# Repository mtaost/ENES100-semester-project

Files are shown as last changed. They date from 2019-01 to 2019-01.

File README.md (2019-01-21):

# ENES100 semester project
ENES 100 is an introduction class for all engineering majors and has students work in teams of 8 to construct an autonomous robotic vehicle to traverse a sand arena and complete a set of tasks. 
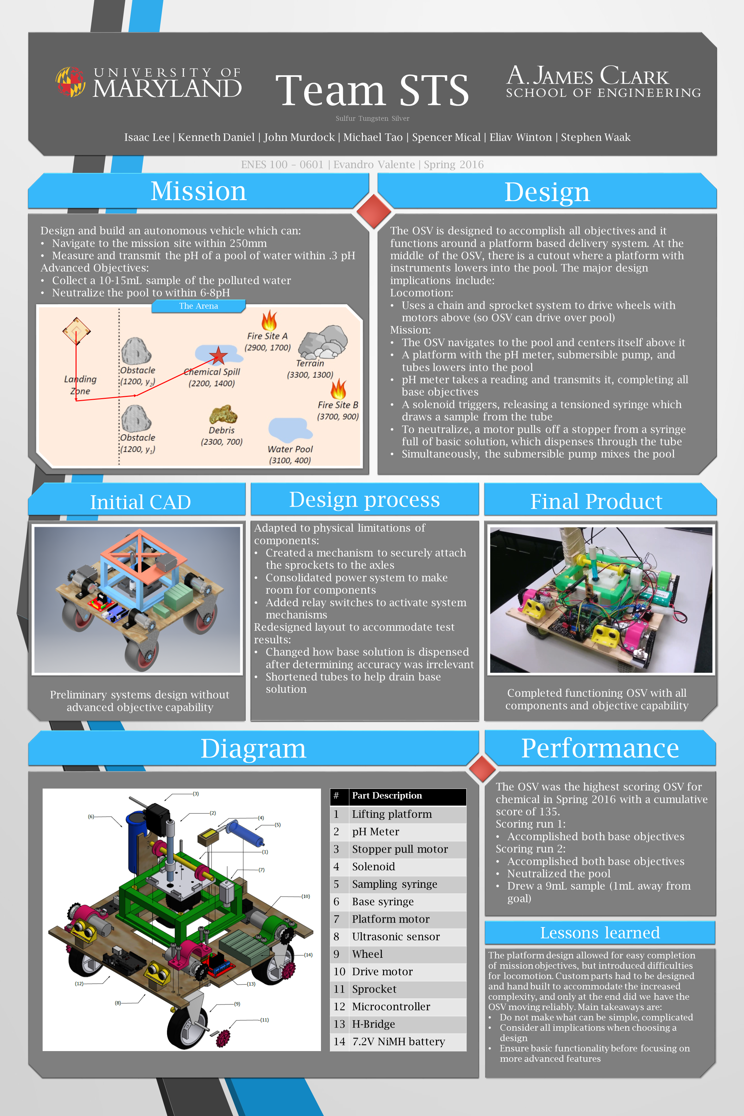
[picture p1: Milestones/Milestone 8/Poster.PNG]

As seen in the poster graphic, the arena was a closed off sandbox with two randomly placed rock obstacles and pre-placed objective sites. Some of the objectives were candles which had to be extinguished or blocks that had to be measured. As our team's mission was the chemical mission, our OSV (On Sand Vehicle) had to:

 - Navigate to the mission objective (a pool of water)
 - Measure the pH of the water and transmit it to the base station
 - Collect a 10-15mL sample of the water
 - Neutralize the pool of water to a pH of 6-8

The class was graded mostly on milestones throughout the class which included presentations and reports detailing our plan of attack as well as the final results. A more detailed description of each milestone can be found at [Milestones/README.md](https://github.com/mtaost/ENES100-semester-project/blob/master/Milestones/README.md) 
My role in this project was team captain so I had a large part in design decisions and task distribution. Ultimately our team succeeded in completing all of our mission objectives.

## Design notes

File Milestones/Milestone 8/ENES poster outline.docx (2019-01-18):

ENES poster outline

- Mission
- OSV details:
  - Locomotion
  - Actuation
- Mission Process
  - How it does the things
  - Control algorithm
- Performance
  - Placement
- Control algorithm
- Design process
  - Initial Cad
  - Final Cad
  - Final picture
- Lessons learned
- Design choices

Executive Summary

Introduction

Shortcomings

Design details:

Structure

Propulsion

OSV Mission

Power

Sensors and Actuators

Control algorithm

Final design drawings

Drawing

Assembly

Circuit diagram

Construction details

Final BOM

Gantt chart

Product performance and evaluation

Lessons learned

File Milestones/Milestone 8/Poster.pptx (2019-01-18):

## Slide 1

Team STS
Sulfur Tungsten Silver

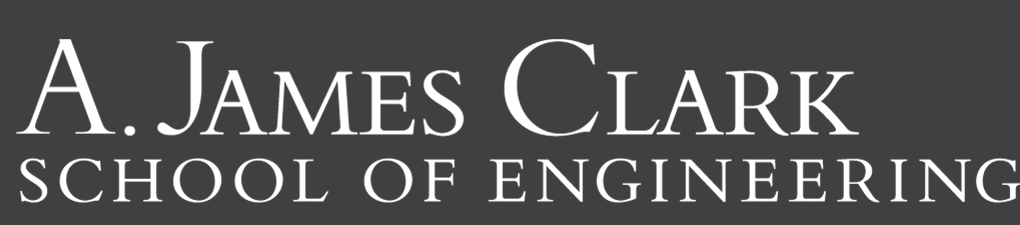
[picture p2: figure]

Isaac Lee | Kenneth Daniel | John Murdock | Michael Tao | Spencer Mical | Eliav Winton | Stephen Waak

ENES 100 – 0601 | Evandro Valente | Spring 2016

Mission

Design and build an autonomous vehicle which can:
- Navigate to the mission site within 250mm
- Measure and transmit the pH of a pool of water within .3 pH
Advanced Objectives:
- Collect a 10-15mL sample of the polluted water
- Neutralize the pool to within 6-8pH

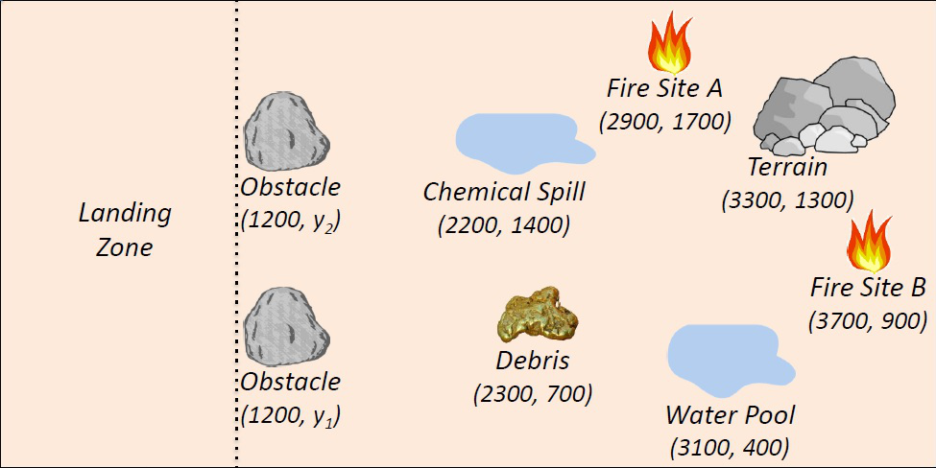
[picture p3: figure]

The Arena

Design

The OSV is designed to accomplish all objectives and it functions around a platform based delivery system. At the middle of the OSV, there is a cutout where a platform with instruments lowers into the pool. The major design implications include:
Locomotion:
- Uses a chain and sprocket system to drive wheels with motors above (so OSV can drive over pool)
Mission:
- The OSV navigates to the pool and centers itself above it
- A platform with the pH meter, submersible pump, and tubes lowers into the pool
- pH meter takes a reading and transmits it, completing all base objectives
- A solenoid triggers, releasing a tensioned syringe which draws a sample from the tube
- To neutralize, a motor pulls off a stopper from a syringe full of basic solution, which dispenses through the tube
- Simultaneously, the submersible pump mixes the pool

Initial CAD

Preliminary systems design without advanced objective capability

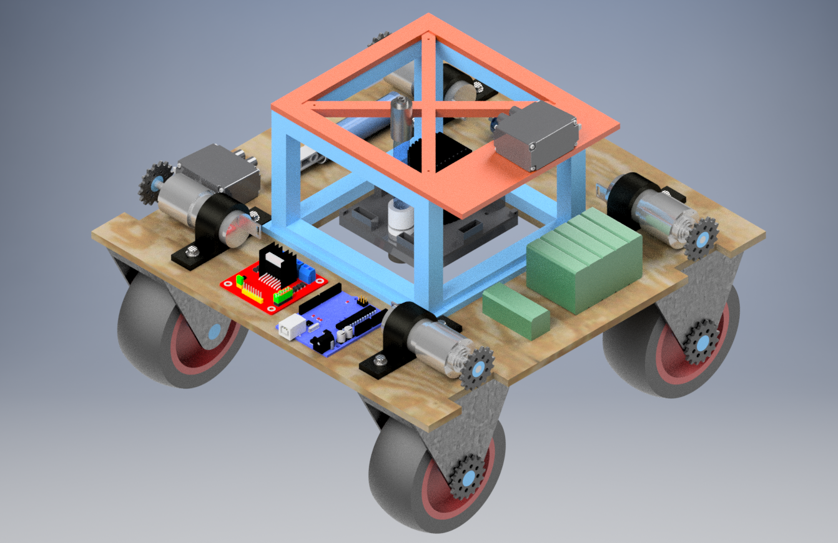
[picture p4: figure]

Design process

Adapted to physical limitations of components:
- Created a mechanism to securely attach the sprockets to the axles
- Consolidated power system to make room for components
- Added relay switches to activate system mechanisms
Redesigned layout to accommodate test results:
- Changed how base solution is dispensed after determining accuracy was irrelevant
- Shortened tubes to help drain base solution

Final Product

Completed functioning OSV with all components and objective capability

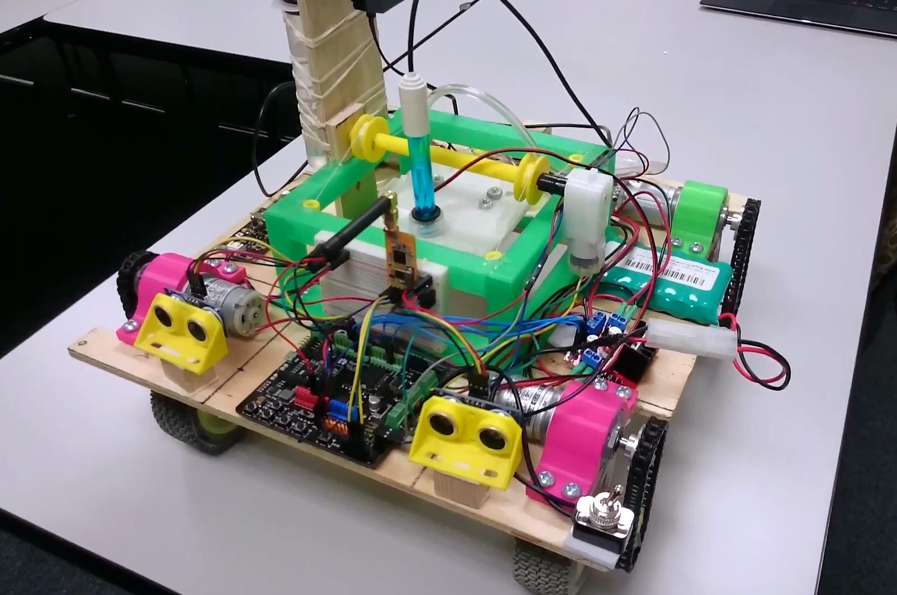
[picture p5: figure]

Diagram

Performance

The OSV was the highest scoring OSV for chemical in Spring 2016 with a cumulative score of 135.
Scoring run 1:
- Accomplished both base objectives
Scoring run 2:
- Accomplished both base objectives
- Neutralized the pool
- Drew a 9mL sample (1mL away from goal)

Lessons learned

The platform design allowed for easy completion of mission objectives, but introduced difficulties for locomotion. Custom parts had to be designed and hand built to accommodate the increased complexity, and only at the end did we have the OSV moving reliably. Main takeaways are:
- Do not make what can be simple, complicated
- Consider all implications when choosing a design
- Ensure basic functionality before focusing on more advanced features

# | Part Description

1 | Lifting platform
2 | pH Meter
3 | Stopper pull motor
4 | Solenoid
5 | Sampling syringe
6 | Base syringe
7 | Platform motor
8 | Ultrasonic sensor
9 | Wheel
10 | Drive motor
11 | Sprocket
12 | Microcontroller
13 | H-Bridge
14 | 7.2V NiMH battery

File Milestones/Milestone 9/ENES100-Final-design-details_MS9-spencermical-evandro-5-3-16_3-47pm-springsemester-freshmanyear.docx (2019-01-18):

Spencer Mical

Team: S.T.S.

Teacher: Evandro

Mission: Chemical Neutralization

Final design details. This should include details of your final OSV design as well as your final mission strategy. Include engineering drawings of the OSV and any components, as well as circuit diagrams as needed to make the description more comprehensible to a reader. Include appropriate calculations and test results either in the body of the section or in an Appendix, as suited for narrative coherence. Include the following subsections.

Structure. Present the size, shape, materials, and construction methods for your structure along with details of your wheel type and suspension. Include estimates or measurements of OSV mass.

Propulsion. Present the sizing and selection of your propulsion system. Include details of wheel or tread size, motor selection, drive train, and steering system design. Provide calculations for the required motor/wheel torque and resulting motor/wheel angular velocity and OSV speed. Provide details of the placement of each of these components. Provide results of performance measurements or tests conducted in the laboratories.

OSV Mission. Identify which mission your OSV attempted and describe your final strategy used to complete the mission. Provide details of the performance of this design strategy.

Power. Present your power system for propulsion and electronic control systems. Describe how you modulated power. Include battery selection details, run-time estimates and actual power subsystem performance.

Sensors and actuators. Present your sensors and actuators, describe how they interact with the Arduino interface, and discuss the rationale for their final placement on your craft.

Control algorithm. Discuss your control strategy and present a flowchart or pseudocode of your control algorithm. In the Appendix, provide the final code generated for your controller. These pages of final code are the only part of the Appendix that do not count towards your 25 page limit. A reader should be able to make sense of how your algorithm functioned.

Final design drawings. Present the following computer-generated drawings with sufficient labels, dimensions and notes. Follow appropriate technical standards. All fonts must be 10 point or larger. Drawings that are appropriate to include within the ‘design details’ section, should be included there. Any that do not fit into the description should be included in this separate section. At the very least, the following three drawings should be included in the report:

- Drawing of OSV structure showing construction detail.
- Assembly drawing of complete vehicle with all components. Clearly identify the location of each component.
- Wiring schematic(s) for all electronic components.

Construction details. Provide the details of the construction materials and processes. Include additional drawings and photos as necessary to allow someone with a similar level of training to regenerate your OSV.

Final design details. This should include details of your final OSV design as well as your final mission strategy. Include engineering drawings of the OSV and any components, as well as circuit diagrams as needed to make the description more comprehensible to a reader. Include appropriate calculations and test results either in the body of the section or in an Appendix, as suited for narrative coherence. Include the following subsections.

Team S.T.S. O.S.V. was designed to meet the maximum parameters of the competition. In doing so, the O.S.V. was designed to have a wide body width and length. This design was purposeful, as it allowed the O.S.V. to drive over the chemical water source, stop on top of the objective, and lower a platform into the pool of water. The body of the O.S.V. has a square-section cut out of the middle, which enables the lifting platform to be lowered from the O.S.V. body to the water, and then raised back up from the water to the O.S.V. body. The lifting platform is attached to a C.A.D.-designed and printed mount/box, which provides support and stability for the lifting platform as it elevates and sinks. Also attached to the O.S.V. body are four motors, each secured to the O.S.V. body by C.A.D. modeled motor mounts. These motors provide power to the four wheels that propel our O.S.V., which are located on the underside of the vehicle.

Pertaining to the mission strategy, team S.T.S. used two ultrasonic sensors, which are mounted to the front of the vehicle. These, along with the control algorithm, enabled the O.S.V. to navigate from the landing zone to the polluted pool, while simultaneously avoiding obstacles. Upon arrival to the pool, the O.S.V. would park over the objective, and would then run a program which controls the crank that raises and lowers the lifting platform. The lifting platform will then be lowered into the water, where all of our base objectives will be met. After successfully navigating to the pool site, and thus accomplishing the first base objective, the lifting platform will then rise back up to the O.S.V. body. The platform will then lower again, and the pH meter will be inserted into the water. At this point, the pH meter will record the pH, satisfying the second basic objective. Upon determining the pH, the pH meter will inform the A.P.C. what the pH is, and then the A.P.C. will transmit the pH to command. After fulfilling the base objectives, additional instruments that are mounted on the O.S.V. body will perform the advanced objectives. There are two syringes attached to the O.S.V.’s body: a 10 mL syringe, which is used to extract a 10 mL sample of polluted water, prior to the team’s neutralization of the pool of water, and a 50 mL syringe, which has a tube attached to it. The 10 mL syringe is constrained by solenoid, which, upon a signal, will retract. Once the solenoid has moved back, the syringe will begin extracting the sample of water, and also completing the first advanced objective. Then, the 50 mL syringe is activated, as part of the second advanced objective of neutralizing the water source. The lifting platform will facilitate a base to be added to the acidic water, via a tube that connects a syringe that’s mounted on the O.S.V. body to the water source. A pump also housed on this platform would be activated, and would agitate the water as the base was dispensed, thus expediting the neutralization process, and accomplishing the second advanced objective.

Structure. Present the size, shape, materials, and construction methods for your structure along with details of your wheel type and suspension. Include estimates or measurements of OSV mass.

Team S.T.S.’s O.S.V. is a square, measuring 350 mm by 350 mm, with a body thickness of 6.13 mm. There is a square hole cut out of the center, as previously mentioned, which allows for the lifting platform to raise up and down.

The O.S.V. body is composed of wood. The majority of the other assembled parts that were subsequently attached to the O.S.V. are either wood, metal, or P.L.A. Wood was used to fasten and secure certain instruments down to the body of the vehicle. Metal was used as a wheel holder to ensure that the wheels are straight and secure, which ensures accuracy in the vehicle’s movement. P.L.A. was used as a result of C.A.D. 3D parts, which were constructed to meet certain parameters and dimensions, and then printed and added to the OSV body.

The O.S.V. weighs approximately 2700 grams without the base solution loaded into the syringe.

OSV Mission. Identify which mission your OSV attempted and describe your final strategy used to complete the mission. Provide details of the performance of this design strategy.

Team S.T.S.’s mission was the chemical neutralization mission. The basic objectives were to navigate to within 250 mm of the polluted freshwater pool, much like the first basic objective of every other group, as we had to navigate to within 250 mm of our objective. Our second basic objective was to measure the pH level of the polluted freshwater pool, and our third basic objective was to transmit that pH level back to command. Our advanced objectives were to collect a 10-15 mL sample of the polluted freshwater source, prior to neutralizing the pool pH to a range of 6 - 8. We would then have to transmit this neutralized pH back to command to complete the second advanced objective.

In the first run, the O.S.V. completed all of the basic objectives. It navigated directly to the polluted freshwater pool after a brief interaction with a boulder. The O.S.V. then proceeded to park atop the polluted freshwater pool, per the group’s design. The lifting platform, containing a pH meter was lowered into the pool, where it acquired and transmitted the pH of the pool back to command. When the O.S.V. attempted to do the advanced objectives, a few things went wrong, and neither of the two were completed. Pertaining to the 10-15 mL sample, the O.S.V. had a syringe that had been stopped by a solenoid. When the solenoid fired, the syringe would retract, and would thus take up water with it. During the first run, the solenoid never fired, so the syringe never extracted water. Regarding the neutralization process, the O.S.V. was intended to administer a sodium bicarbonate base to the acidic pool. However, the base was added to the O.S.V. too early, and it solidified on the bottom of the syringe, thereby blocking any flow of water or base into the pool. All in all, the O.S.V. received a 60/60 for performing all of the basic objectives.

For the second run, things went much better. Again, the O.S.V. accomplished all of the basic objectives. It successfully navigated to the polluted freshwater pool, after temporarily getting stuck on a boulder. Through sheer power, the O.S.V. broke past, and went on to complete the mission. The O.S.V. stopped over the pool, and once again lowered the lifting platform into the water. The pH meter recorded and transmitted the pH of the acidic pool back to command, thus securing another perfect basic objective performance. However, the O.S.V. then went on to successfully complete the two advanced objectives as well. The solenoid fired properly this time, as an acceptable sample of water was collected (up to debate between the judges and our team). Additionally, the neutralization process went according to plan. The base was administered to the O.S.V. moments before the second run began, so it wouldn’t have time to settle and solidify. The syringe with base released a pre-measured amount of base and water into the pool, where the pH of the pool was neutralized from a pH of 2.99, to a pH of 6.31, thereby successfully completing the second advanced objective.

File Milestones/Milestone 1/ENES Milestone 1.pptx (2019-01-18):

## ENES Milestone 1

Team STS (Sulfur Tungsten Silver)

## Team Roster

- Isaac Lee (The neutralizer)
- Kenneth Daniel (Canned denial)
- Michael Tao (Chairman Tao)
- John Murdock (John Cena)
- Eli Winton (Wins a ton)
- Spencer Mical (One man army)
- Stephen Waak (Woah, OK)

## Mission objectives

- Chemical Team:
  - Base Objectives:
    - Navigate to within 250 mm of the polluted freshwater pool
    - Measure the pH level of the pool
    - Transmit to command the pH level to within 0.3 units
  - Advanced Objectives:
    - Collect a 10 – 15 ml sample of the polluted water prior to neutralization
    - Neutralize the pool by returning the pH level to the range of 6 - 8 and transmit to command the final pH level

## Team Structure

Project Leader: Michael Tao
- Subgroups:
  - Mechanical : Isaac Lee
    - CAD: Kenneth Daniel
  - Electrical: John Murdock
  - Programming: Michael Tao
Meeting arrangements:
  - After class in JMP on Thursday
  - Otherwise, Hornbake or McKeldin

## Design Concepts - Structure

- 4x4 design without suspension
- Wheel width and diameter is being determined with respect to desired torque
- Designing base for maximum size (350mm x 350mm)
- Wooden base platform, 3d printed support

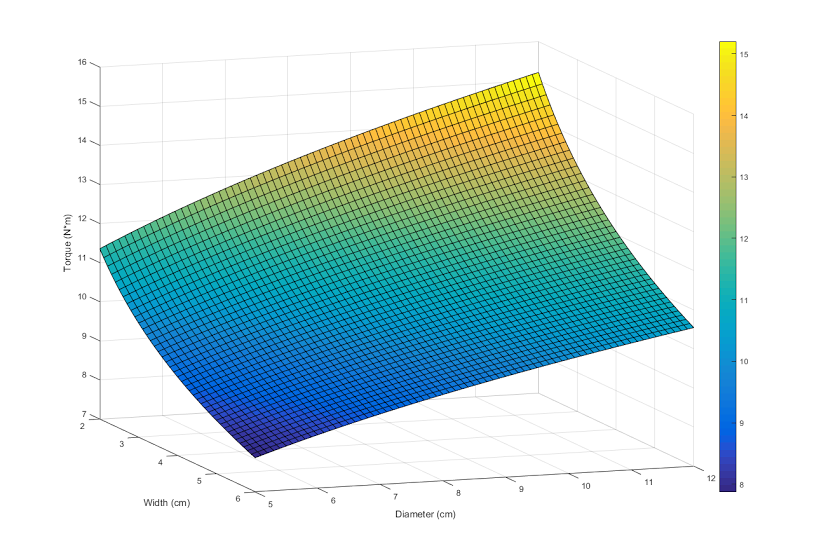
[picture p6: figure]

## Design Concepts - Structure

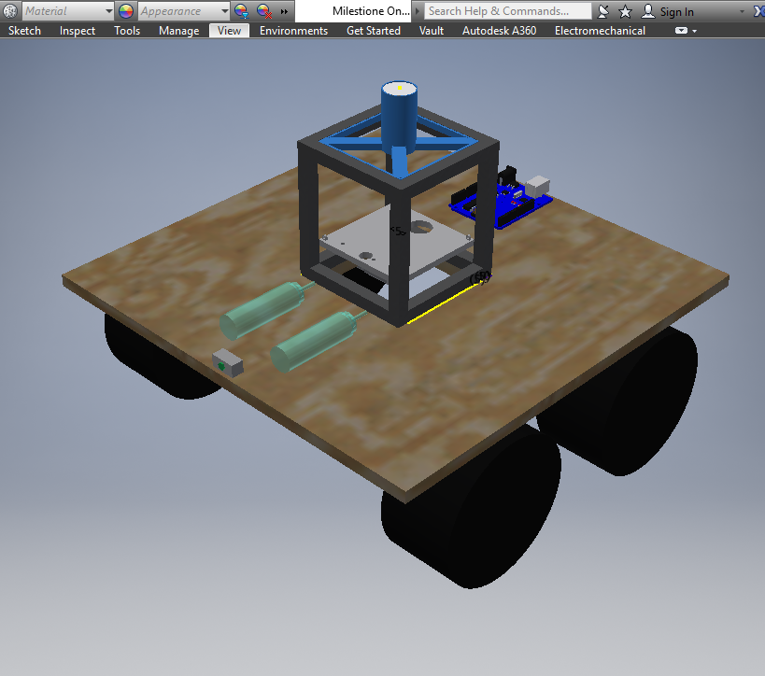
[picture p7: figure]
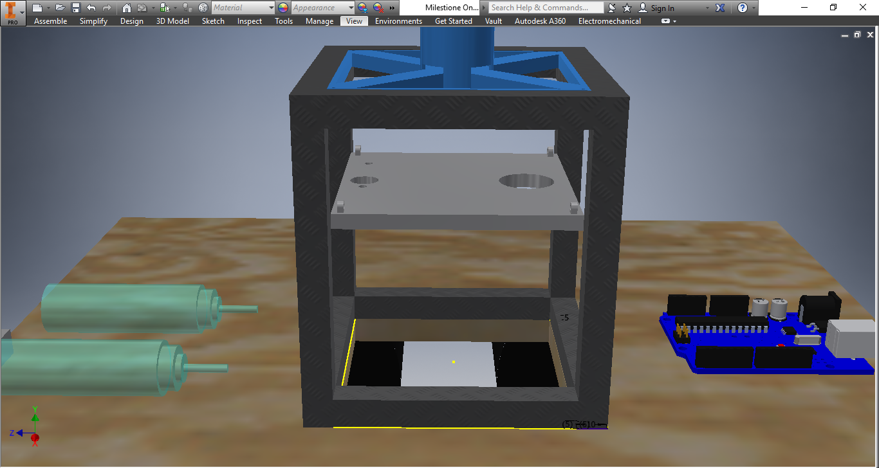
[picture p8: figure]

## Design Concepts - Mobility

- Torque required in one rear wheel τ=TE∙r TE=C_(RR) ∙F_N C_(RR) =[3.33(cm^3)/N∙(F_N)/(w∙d^2)]^(1/3)
F_N =(lmgcosθ+hmgsinθ)/(4l)
r = wheel radius
w = wheel width
d = wheel diameter
h = height of center of mass
m = mass of OSV
g = acceleration due to gravity
ϴ = angle of inclination
l = horizontal distance from contact point to center of mass

## Design Concepts - Mobility

- Using assumed values, r = 6.4cm w = 6cm d = 12.8cm h = 10cm m = 2.5kg g = 9.8 m/(s^2) 30° < ϴ < 40° l = 11.1cm  15.54 N∙cm<τ<15.99 N∙cm Minimum torque required for rear wheel rotation up an incline

## Design Concepts – Avoiding The Dig

0.3F_N <TE<0.7F_N
0.3F_N ∙r<τ<0.7F_N ∙r
The limiting scenario would be at 0°
Using previous assumptions,
11.76 N∙cm<τ<27.44 N∙cm
Torque range required to not dig sand at 0°
15.99 N∙cm<τ<27.44 N∙cm
Torque range required to move up 40° inclines but not dig sand at 0°

## Design Concepts - Mobility

- Based on our calculations of our range of τ , we have found 2 motors that fit our needs, both of the same form factor but with a different transmission
- Both are planetary

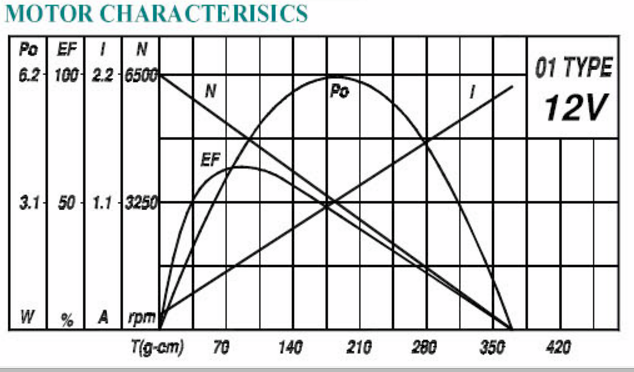
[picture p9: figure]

## Design Concepts - Mobility

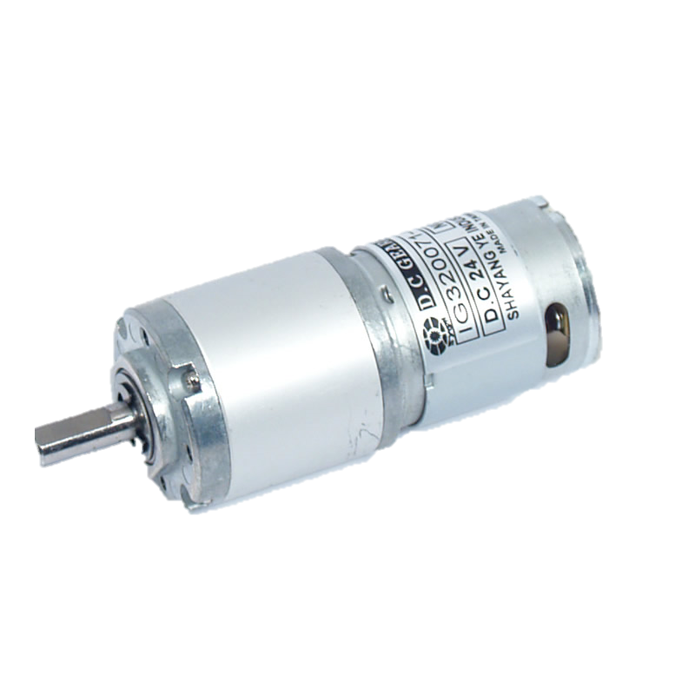
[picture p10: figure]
IG32 12VDC 104 RPM Gear Motor

Torque: 45.08 N*cm
RPM: 53
Gear ratio: 1:100
Voltage: 12V
Max I draw: 530mA
Mass: 190g

Torque: 22.54 N*cm
RPM: 104
Gear ratio: 1:51
Voltage: 12V
Max I draw: 530mA
Mass: 190g

## Design Concepts - Power

- At maximum power, both of the motor choices will draw 530mA, so max current of 4 motors is 2.12A
- Assuming the other systems draw 100mA, we have a total current draw of 2.22A
- If we want a run time of 1 hour, we need a battery at 12V with a capacity of at least 2.22Ah

## Design Concepts - Power

- 12 V 2200mAh battery with built in short circuit protection

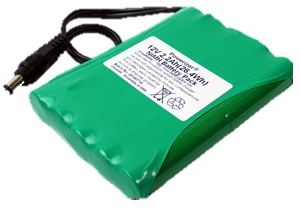
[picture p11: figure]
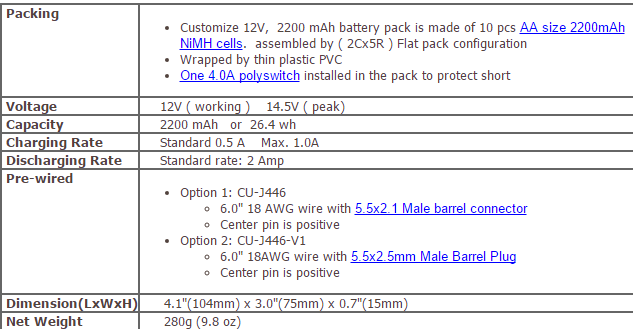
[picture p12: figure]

## Design Concepts – Mission performance

- Platform driven directly over pool to perform mission objectives
- pH probe on platform to be lowered into pool
- Motor driven syringe to obtain sample
- Motor driven syringe to inject neutralizer solution
- Electric submersible pump to agitate solution
- Closed feedback loop to neutralize solution to pH 7

## Design Concepts - Navigation

- Differential drive with the 4x4 motors
- Using an array of ultrasonic sensors to locate obstacles
- Contact sensors or color sensors underneath the OSV to detect the pool of water

## Gantt chart

## Anticipated problems

Problems
- Inability to focus on task during meetings
- Individual tasks not being completed by deadline
- Electronics malfunctioning (Releasing magic smoke / mechanical failure)

Solutions
Create defined goals for each meeting
Enact consequences for failing to meet deadlines (Voluntary sponsored pizza dinner)
For cheaper parts, always buy an extra. Have someone else check wiring before powering on

## Anticipated problems

Problems
- Member unable to contribute due external reasons
- Unequal work distribution

Solutions
Redistribute tasks to best ability
Discuss how work could be divided evenly but still adhere to standards

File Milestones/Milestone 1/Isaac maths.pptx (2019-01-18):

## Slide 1

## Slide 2

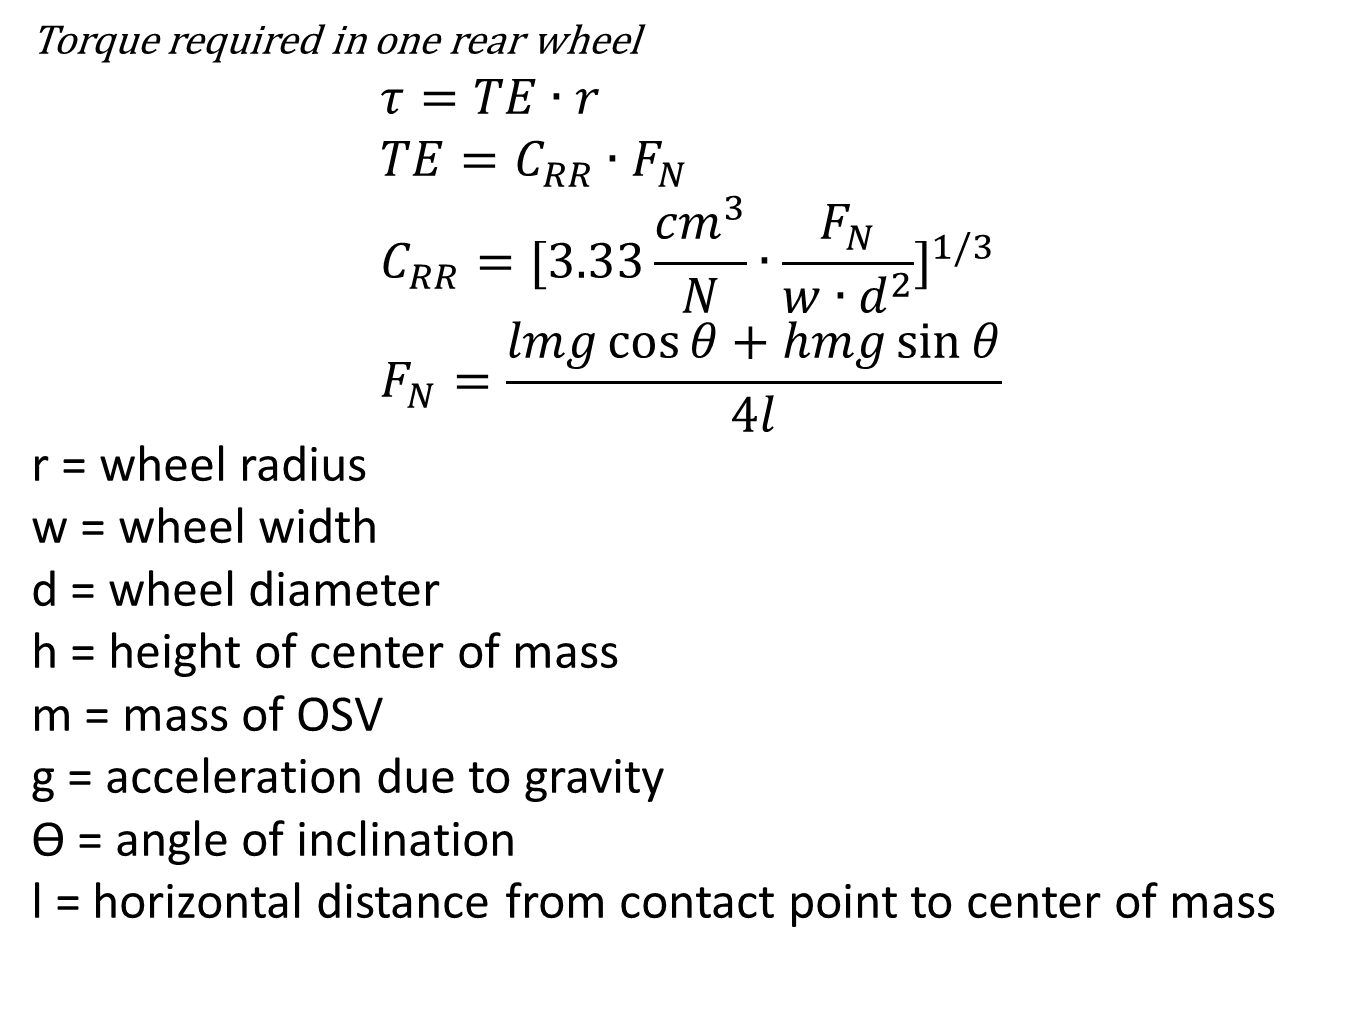
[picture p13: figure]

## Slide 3

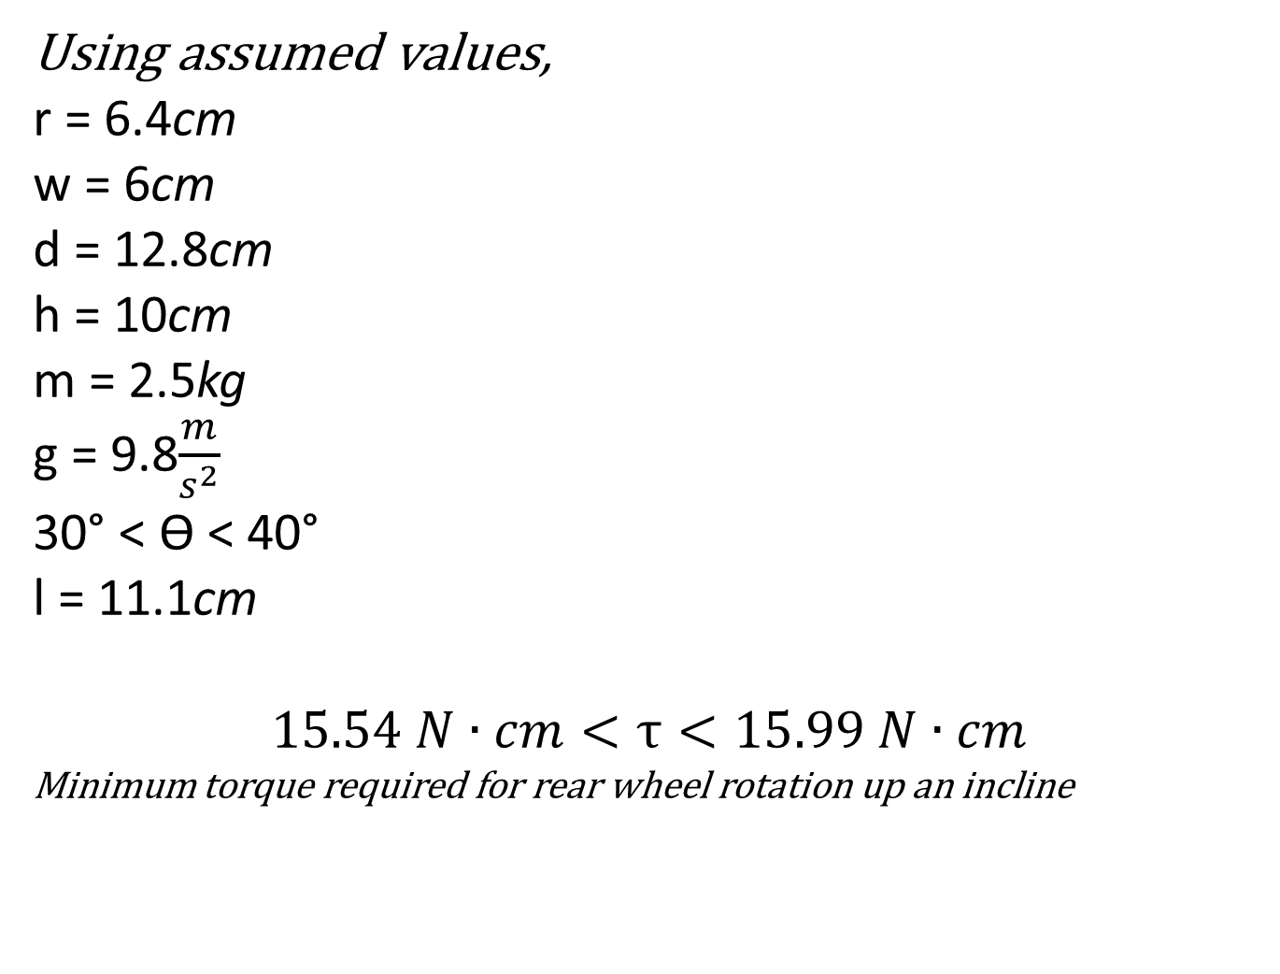
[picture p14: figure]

## Avoiding The Dig

0.3F_N <TE<0.7F_N
0.3F_N ∙r<τ<0.7F_N ∙r
The limiting scenario would be at 0°
Using previous assumptions,
11.76 N∙cm<τ<27.44 N∙cm
Torque range required to not dig sand at 0°
15.99 N∙cm<τ<27.44 N∙cm
Torque range required to move up 40° inclines but not dig sand at 0°

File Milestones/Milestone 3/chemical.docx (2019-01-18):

For our chemical neutralization mission our primary objective is finding and neutralizing a pool of water within the given amount of time. We are required to navigate within 250 millimeters of a polluted fresh water pool with the water being between 650 and 850 milliliters and the pollution being between 2 and 5 pH. Once we reach the pool we must measure the pH level of the pool and report back to command the pH level to within 0.3 units. After testing the pH level we must then extract a 10-15 milliliter sample of the polluted water. Once we have successfully collected the sample of water we can then begin to neutralize the pool and bring the pH level back to between 6 and 8 and report our level to the command.

To navigate to the pool, we will use distance sensors and angular turning to navigate around the obstacles. After the obstacles are cleared, the OSV will drive to the coordinates of the pool. Once over the pool, the OSV will lower the inner platform into the pool. From here it will extract the sample of the polluted water, measure the pH of the pool, and send the pH reading back to base. After this part is complete, the OSV will dispense the fully saturated sodium bicarbonate solution until the pH of the pool reaches 6 using a closed feedback loop. While the base is being dispensed, the pump will be agitating the pool to mix in the base. Once the pH meter reads a pH within the range of 6 to 8, the OSV will stop dispensing base and will report the measured pH to base.

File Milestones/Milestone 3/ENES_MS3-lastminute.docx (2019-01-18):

The O.S.V. is approximated to be at the full 350 mm by 350 mm, although if it can be slimmed down a bit that will be attempted. The O.S.V. will feature a wooden platform that measures 350 mm by 350 mm, and upon that will be everything that the O.S.V. needs to operate. The O.S.V. will include four motors, an Arduino Romeo board, and an H-Bridge to connect a 12 volt battery to the wheels. A 7.2 volt battery will provide power to the rest of the O.S.V.

The O.S.V. has a box-like structure. The main body platform is a large square. On top of that, at the center of the large square, is a hollowed out cube, which houses and will help operate the lifting platform.

The O.S.V. will be constructed over several weeks. Parts will be added meticulously and cautiously, in order to ensure that they are placed accurately and are securely fasted/attached to the O.S.V.

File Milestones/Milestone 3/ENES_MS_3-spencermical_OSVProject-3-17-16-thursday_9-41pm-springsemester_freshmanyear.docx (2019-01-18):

ENES MS 3

For Spencer’s portion of MS 2 and MS 3, Spencer worked on CAD designs and doing some research on the chemical aspects of the O.S.V. project. Spencer also took measurements to determine the mass, volume, and areas, of multplie components of the O.S.V. Additionally, Spencer and Isaac came up with the idea that the O.S.V. would drive and park over the polluted water source, and then lower the pH and base solutions into the water.

Ken would dimension parts for the O.S.V. that had to be CADded, and Spencer would CAD them. Ken and Spencer about equally split the amount of CADding for the O.S.V., but Ken is the one who assembled all of the parts together to make one-coherent viewing of the O.S.V. as it is in the presentation. Ken would give Spencer an idea of a part that the O.S.V. needed, and Spencer would create it. Otherwise, Ken would give Spencer dimensions or other parameters that needed to meet O.S.V. specifications, and Spencer sought out to create a part that could fit those dimensions. After Spencer created the part, Spencer would then determine the area, volume, and estimated mass of these parts, given the density and mass of polylactic acid (P.L.A.). That way, the group could have a decent idea of how much everything would weigh, and therefore could stay within the given parameters of the project. There were also times where Ken gave Spencer dimensions for a part that would later either be scrapped, or re-written/constructed, with new dimensions. Either Ken or Spencer would create this new part. This dynamic duo came through clutch with the CADding for this O.S.V. Although the O.S.V. is currently slightly over the permissable mass, this will be resolved by reducing the battery capacity.

Pertaining to the chemical portions of the project, Spencer determined the density, molarity, molar masses, normality, substance pH, and chemical composition. Based on Spencer’s calculations, this aided Stephen in the chemical portion of the project. Stephen would go on to determine how many grams of base the O.S.V. would need to neutralize varying concentrations of acetic acid in the polluted water environment.

One of Spencer’s initial sketches included a diagram that depicted the O.S.V. lowering the pH indicator and the base dispensor into the water. Isaac, too, initally had this idea. The two of them convinced the group that this was plausible, and left little room for error in approaching the water source (i.e. getting to within 250 mm of the objective wouldn’t be difficult). This is the approach that the group has chosen to operate with. Some difficulties may include interference with the wheel motors and the water-source, but this is to be remedied by sticking the motors on top of the platform.

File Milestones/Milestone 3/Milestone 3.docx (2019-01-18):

ENES 100

Section 0601

Milestone 3

Team STS - Chemical

Table of Contents

Page
2 | Team contributions
3 | Executive Summary
4 | Introduction
5-6 | Design: Structure
7-11 | Design: Propulsion
12 | Design: OSV Mission
13-15 | Design: Power
16 | Design: Sensors and actuators, Control algorithms
17 | Design: Control Algorithms
18-22 | Preliminary Design Details
23 | Bill of materials
24 | Gantt chart
25 | Construction plans and anticipated difficulties

Team contributions

John Murdock

Stephen Waak

Eliav Winton

Spencer Mical

Kenneth Daniel

Isaac Lee

Michael Tao

Executive Summary

Our team has designed a vehicle to carry out the chemical neutralization of a pool of water in a sandy terrain. The OSV must fit within a 350mm x 350mm footprint. Overall mass must not exceed 3kg and overall cost of the OSV can be at most $350. With these constraints in mind, we have designed an OSV with four wheels and a lowering platform which will drop into the pool of water to carry out its mission.

For mobility, we have a four wheeled footprint driven by a chain and sprocket. Motors will be mounted above the base of the platform to avoid impacting the pool of water. This will keep the motors safe from the acid pool and leave enough clearance for the bottom. Through control algorithms and sensors, the OSV will navigate autonomously to the pool while avoiding obstacles along the way.

Once the OSV has driven over the pool, it will lower a platform to carry out its mission objectives which include taking a sample, transmitting the pool’s pH, and neutralizing the pool.

Introduction

To fulfill the chemical mission objectives of measuring the pH of a pool, taking a sample, and neutralizing the pool, team STS has designed an OSV that can accomplish these tasks. Locomotion is enabled with four planetary geared motors running at 12v. Each of these motors is mounted atop a wooden base which will serve as the platform for all electronics including microcontroller, motor driver, batteries, and mission specific equipment. Four wheels mounted underneath the platform are connected to sprockets and will be driven through chain by the drive motors. This is to ensure that there is enough clearance beneath the OSV to drive over the pool. Drive motors are driven by a 12v NiMh 2200mAh battery, while microcontroller logic will use a separate 7.2v NiMH 2200mAh battery.

In moving to the mission site, the OSV will navigate using information provided through the APC220, a radio communication module. For obstacle detection, three ultrasonic sensors will be mounted on the front of the OSV so it can detect obstacles in a 45 degree cone in front of it. Through control algorithms, it will avoid obstacles while navigating to the site by determining any obstacles ahead of it and where they are based on proximity.

Once the OSV navigates to the mission site, it will deploy a platform with instruments used to fulfill mission objectives. This platform is held in the center of the OSV and will be further described in technical drawings. On this platform are the pH meter, a pump, and two tubes used to dispense neutralizer, and extract a sample. First, this platform will lower using a smaller geared motor. Then, a sample will be drawn by releasing a spring loaded syringe. Simultaneously, the pH will be read and transmitted back to base through the APC220. Once the base mission objectives are fulfilled, it will then begin dispensing neutralizer. The rate at which the neutralizer is dispensed will be proportional to the difference between desired and actual pH. During this period, the pump will be powered to agitate the solution, thus accelerating the neutralization process and allowing for a more accurate measurement. Once the pool is within acceptable pH ranges, the OSV will have completed all objectives.

Design Details

Structure

The O.S.V. is approximated to be constructed at the full 350 mm by 350 mm and then sanded down to allow for a safe margin. The O.S.V. will feature a wooden base that spans this square, and on this base will be the electronics for locomotion and mission specific hardware. Electronics will be secured to the base with screws where possible and mounting brackets if needed. Any 3d printed parts will be secured using wood glue after properly scoring both contact surfaces to allow for proper adhesion.

Our wheels will be 4-inch diameter rubber tires mounted upon 3d printed wheel inserts. These wheels feature small indentations which will help the wheel grip on to the sand better, and they will be attached to sprockets. The motors will then drive the wheels through a chain. We will not use suspension because of cost and complexity.

The O.S.V. has a box-like structure. The main body platform is a large square. On top of that, at the center of the large square, is a hollowed out cube, which houses the lifting platform and allows for its vertical movement. This platform and the supports will be 3d printed which will allow for lightweight construction yet still maintaining structural rigidity.

Mass estimation table

Item | Mass (g) | Quantity | Total mass (g)
12V battery | 280 | 1 | 280
7.2v battery | 125 | 1 | 125
Vex Motor | 87.1 | 1 | 85.5
Sprockets | 2.8 | 8 | 22.4
Base Solution | 150 | 1 | 150
Wooden base | 400 | 1 | 400
Pump | 50 | 1 | 50
pH monitor | 20 | 1 | 20
Lifting Platform | 33.8 | 1 | 33.8
Arduino | 20 | 1 | 20
Wheels | 10 | 4 | 400
Motor | 160 | 4 | 640
Platform counterbalance | 50 | 5 | 250
Total | | | 2565.4

Propulsion

Στ=Iα

F_T ∙r-τ_w =0

F_T ∙r=τ_w

R_x

R_y

τ_w

m_w g

F_(RR)

F_T

F_N

Figure 1. Torque equilibrium. Resultant of F_N and F_(RR) points directly at wheel center

R_x

R_y

τ_w

m_w g

F_(RR)

F_T

At constant velocity,

X:ΣF=ma

F_T -F_(RR) =0

F_T =F_(RR)

F_N

Figure 2. Horizontal forces equilibrium. τ_w , R_y , R_x , m_w g are internal forces.

l

h

mg

F_(Nr)

F_(Nf)

F_(τr)

F_(τf)

x

y

F_(RRr)

F_(RRf)

l

θ

At stall,

X: ∑ F=ma 2F_(τr) +2F_(τf) -mgsinθ-2F_(RRr) -2F_(RRf) =0

Y: ∑ F=ma 2F_(Nr) +2F_(Nf) -mgcosθ=0

Torque from contact point of front wheels

τ :∑ τ=Iα lmgcosθ+hmgsinθ-4lF_(Nr) =0

Figure 3. Equilibrium equations for OSV stalling on an incline.

τ=F_(τr) ∙r

F_(τr) =F_(RR) =C_(RR) ∙F_(Nr)

C_(RR) =[3.33(cm^3)/N∙(F_(Nr))/(w∙d^2)]^(1/3) F_(Nr) =(lmgcosθ+hmgsinθ)/(4l)

Equation 1. Stall torque in one rear wheel on an incline.

TE<0.7F_N

τ<0.7F_N ∙r

Equation 2. Tractive effort and torque maximum to avoid digging into the sand.

RPM(τ)=-65/219τ+65

Figure 4. Motor Torque vs RPM found by converting the motor’s data sheet using a reductioin ratio of 100 and an efficiency of 60%.

It was decided that the wheels must be 3d printed because the design calls for a very narrow range of dimensions that could not be fulfilled by any wheels on the market. The wheel dimensions were chosen to allow the OSV to clear the pool of water and take the platform above the water. The diameter was calculated with the height of the pool in mind, and the width was calculated with the dimensions of the OSV versus the diameter of the pool in mind. The width was optimized for sliding over sand while still allowing the OSV to drive over the pool. It was decided that the diameter of the wheels would be 107mm and the width 44mm. The wheels will be placed 11.15cm away from the center of mass, measured in the direction of motion, and 1cm inward from the edge of the OSV to allow for the chain and sprocket system. They will be housed in two-sided wheel housings to hold them in the same orientation.

The torque calculations were derived with the models depicted in figures 1, 2, and 3. Equation 1 was used with the following dimensions: a radius r of 5.35cm, a width w of 4.4cm, a diameter d of 10.7cm, a height h of the center of mass of 11cm, a mass m of 3kg, an acceleration g due to gravity of 9.8 m/(s^2) , an angle of incline ϴ of 35°, and a length ℓ between the center of mass and center of a wheel of 11.15cm. Using this equation, the minimum torque per wheel required was determined to be 22Ncm. Using equation 2, the maximum torque that could be output to avoid digging into the sand was found to be 27.5Ncm at 0°. Only the scenario with a 0° incline was considered because it was determined that the wheels digging on an incline would not be a problem. The digging would reduce the incline since the front wheels would begin to dig the sand before the rear wheels. Using these parameters, a 12V motor with a rated torque of 46Ncm was chosen. Each wheel would have its own motor. The motor has a variable torque and angular velocity. Since the maximum torque required for OSV operation is lower than the torque at which the wheels begin digging the sand, it was determined that this motor would always operate under the torque for digging, yet always be able to provide enough torque to overcome the sand and any inclines of the sand.

The drive train was designed with the platform mechanism in mind. It was determined that the motors and wheels must be separated so that the motors would not be in the way of the OSV successfully getting over the pool. To achieve this, the four motors would be placed on the base of the OSV and drive the wheels using a system of chains and sprockets. The sprockets would be sized at around a 1:1 ratio initially but, because of the need to reduce OSV velocity, may end up being around a 1:3 ratio. The chains and sprockets would be oriented to the outside of the OSV, so that there will be maximum clearance on the inside to fit the pool between the wheels. Using the torque vs. RPM graph in figure 4 and a wheel radius of 5.35cm, the range 32.7(cm)/s≤v≤34.1(cm)/s was obtained for OSV velocity for between operation at 35° and at 0°, with 1:1 sprockets. With a wheel sprocket that is 3 times wider than the motor sprocket, a theoretical mechanical advantage of 3 is introduced. This means that the torque output is 3 times the torque input and the angular velocity output is one-third the angular velocity input. The wheel would still need the same torque to overcome its resistance, so the motor would output much less torque. This would increase the angular velocity of the motor because angular velocity is inversely proportional to torque. However, as seen in figure 4, reducing the torque by a third does not increase angular velocity threefold because the two quantities are related by a constant. Overall, this design is expected to reduce the angular velocity, and thus the OSV velocity, by approximately 50%, while lightening up on motor current draw due to the lower motor torque requirement.

The steering system will be differential steering and not require any servos. It will turn by adjusting the relative speeds of the different wheels. Pulse-width modulation will be used to lower the angular velocity of certain motors. This can be performed at the motor bridge and be controlled by the Arduino. PWM can be used to proportionally lower the effective current and voltage that is applied to the motor. The motor will then draw more current at the battery to produce the same torque, but its voltage will be lower and be constant. Torque is directly proportional to current because current produces the magnetic field inside the motor that drives the motor shaft. However, angular velocity is directly proportional to voltage because motor voltage is used to overcome the counter-electromotive force produced by the rotor spinning through the motor’s magnetic field. The motors that need to slow down will be fed lower voltage and therefore output a lower angular velocity at the cost of requiring higher current draw to produce the same torque. However, this will not impact battery capacity requirements because the increased current draw is balanced out by the <100% duty cycle, and total power draw will be roughly the same.

OSV Mission

For our chemical neutralization mission, our primary objective is finding and neutralizing a pool of water within a five minute window. The OSV is required to navigate within 250 millimeters of a polluted water pool with the water being between 650 and 850 milliliters and the acidity being between 2 pH and 5 pH. Once it reaches the pool we must measure the pH level of the pool and report back to command the pH level to within 0.3 units. After testing the pH level it must then extract a 10-15 milliliter sample of the polluted water. Once we have successfully collected the sample of water we can then begin to neutralize the pool and bring the pH level back to between 6 and 8 and report the newly adjusted pH to the command.

To navigate to the pool, the OSV will use distance sensors and differential steering to navigate around the obstacles. After the obstacles are cleared, the OSV will drive to the coordinates of the pool. Once over the pool, the OSV will lower the inner platform into the pool. From here it will extract the sample of the polluted water, measure the pH of the pool, and send the pH reading back to base. After this part is complete, the OSV will dispense the fully saturated sodium bicarbonate solution until the pH of the pool reaches 6 using a closed feedback loop. While the base is being dispensed, the pump will be agitating the pool to mix in the base. Once the pH meter reads a pH within the range of 6 to 8, the OSV will stop dispensing base and will report the measured pH to base.

Power

For our power system, we used two separate batteries. The battery that we will be using to power the Romeo Board is a 7.2V 2200mAh NiMH battery. This will provide power for all mission specific hardware. The battery that is used to power the wheel motors is a 12V 2200mAh NiMH battery. These batteries were chosen because they are able to supply power within the operational limits of the electronics necessary for function and sustain that power for a long enough time.

The 12V battery will connect to the H-bridge that connects to the four drive motors. Calculating the current draw of the four motors used to power the wheels in the OSV is dependent on the amount of torque that is required in each of the wheels. As previously stated, the amount of torque required will depend on the angle of the wheel the motor is attached to with respect to ground level. Once this is known, determining the current can be done by using the equation:

i = mτ + b

Equation 3. Current draw at a given motor torque

In this equation, i is the current draw, m is the motor torque constant which is equal to 11.78mA/Ncm or the max current of 530mA divided by the stall torque of 45Ncm, τ is the torque, and b is the no load current of 150mA. This allows us to determine the range of currents that are possible. Based on the previous torque calculations:

Minimum torque required: 14.3Ncm

Maximum torque required: 22.2Ncm

And using equation 3 to find the minimum and maximum current draws:

Minimum motor current draw: 318mA

Maximum motor current draw: 411mA.

Because there are four separate motors,

Minimum 12v battery draw = 1272mA

Maximum 12v battery draw = 1644mA

Taking these numbers into consideration, we found a battery that can sustain this current draw. Capacity is given by the equation:

C = I * hr

Equation 4. Capacity of a battery in amp hours

Thus, by substituting in battery capacity, min and max current draws, we calculate that:

Minimum battery life = 1.34 hours or 80 minutes

Maximum battery life = 1.73 hours or 104 minutes

To prevent damaging the battery, %20 of the battery capacity is reserved, and assuming maximum current draw for the entirety of the run time means that the calculated battery life is:

Battery run time = 64 minutes

As previously stated, the 7.2V battery will be used to power all the other functions on the OSV and this battery will be plugged directly into the Romeo Board. The Romeo Board will in turn be wired and connected with the various parts of the OSV to provide them power. The only exception to this will be the APC-220, which will be plugged directly into the Romeo Board. In order to determine the runtime of this battery, we had to calculate the total current that would be drawn by the various parts of the OSV that the Romeo Board is wired into. To do this we checked the data sheets for the parts for their standard current draw. We then summed these numbers up and divided them into the 2200mAh that we knew this battery would provide.

Expected battery draw of mission specific equipment

APC: 42mA

Romeo board: 300mA

3x HC-Sr04 Ultrasonic sensor: 45mA

Brushless water pump: 400mA

Lifting platform: 150mA

Vex motor (at expected torque and using Eq. 3): 1.2A

Summing up these currents yields a maximum concurrent current draw of 2.1A. If we assume that all of these components will run at full for the entire time, through Eq. 4, we yield a run time of 1.02 hours. In practice, the run time will be much higher because the components will only run for a small portion of the time the OSV is active. Specifically, during the completion of mission objectives.

Sensors and actuators

The OSV will receive location data including the position and orientation of the OSV, and the position of the objective through the APC220. Using this data, it will use control algorithms to avoid obstacles. The three ultrasonic range sensors are mounted on the forward facing side of the OSV. One will point directly towards where the vehicle is heading, and the other two will be off to a 45 degree angle. In this configuration, the OSV will be able to tell exactly where obstacles are in front of it. For example, if the sensor pointing 45 degrees right indicates an object approaching, the OSV knows that somewhere off to the right, there is an obstacle. A small course adjustment can be made to ensure no contact. However, if both the right pointing and forward pointing sensors indicate an obstacle, the OSV knows that the obstacle is obstructing the path more. Then, a larger correction would be made to avoid the obstacle.

One actuator will be one motor on a worm gear and rack system. This will provide adequate linear force to depress the syringe and dispense base slowly and precisely. A solenoid will be used to retract and allow a spring driven syringe to extract a set volume of fluid for sampling purposes. The final actuator is simply a motor atop the platform. When powered, it will slowly lower the platform allowing for a controlled deployment of mission hardware.

Control Algorithm

The proposed methods for locomotion are as follows:

turn(angle)

moveForward(x, spd)

moveBack(x, spd)

detect(sensor)

These fundamental functions will allow the OSV to move, and a more complex algorithm will implement these methods to allow the OSV to navigate precisely within its environment. For example, the OSV would first calculate the x position of the target, and turn towards that heading given its initial position. Then, it would continuously detect any obstacles along the way and make adjustments accordingly, utilizing turning, moveFoward, and moveBack if it finds itself stuck.

Once the mission site is reached, the OSV will use these methods to carry out the mission objectives:

lowerPlatform()

getSample()

readpH()

transmit(pH)

neutralize(pH)

-readpH()

-dispenseBase(mL)

-agitate(duration)

-delay(ms)

These methods are listed in order in which they will be called, and adequate time will be given to allow the hardware to make accurate measurements. For neutralization, a closed feedback loop will allow neutralization to a precise pH by continuously measuring pH, and dispensing a proportionate volume of neutralization solution. Then, it will agitate the solution to allow for a more accurate measurement, as well as accelerating the neutralization process. Once this has reached a satisfactory pH, the OSV will finally transmit the ending pH of the pool.

Preliminary Design Details

OSV Configuration:

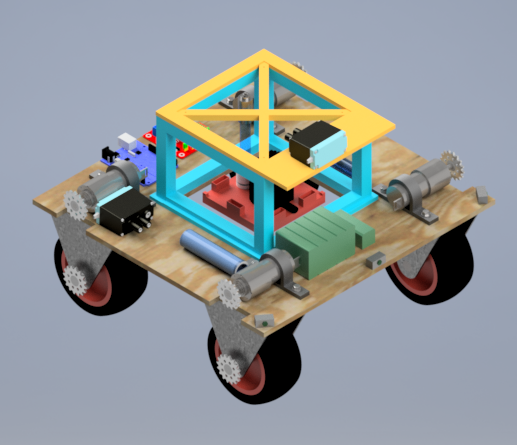
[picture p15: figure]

Motor Mount

Distance Sensor

Gear Sprocket

Base Syringe

Steel Wheel Mount

Romeo Board

12V DC Motor

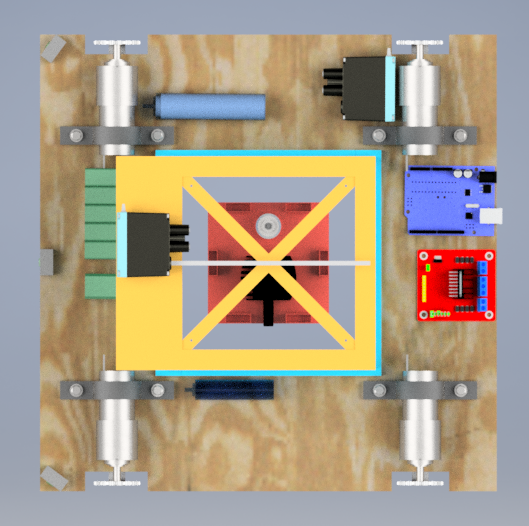
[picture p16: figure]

Counter Balance Slot

Agitation Pump

pH Monitor

Vex Motor With Pulley System

Base Syringe

12V and 7.2V Battery

L298 Duel H-Bridge

Sampling Syringe

Design Overview: To complete the chemical mission, this OSV is designed to maneuver about the chemical spill. Once in place, a pH monitor, agitation motor, and needed tubing will be lowered to titrate the pool.

- To maximize the allowance of error in maneuvering, this design is uses the maximum base dimension of 350x350mm and a suspension height of 127mm. To drive over the chemical spill with a diameter of 190mm, clearance space become a concern. With maximum dimensions, tolerance in navigation is permitted lessening the likelihood of the vehicle getting stuck while maneuvering over the spill.

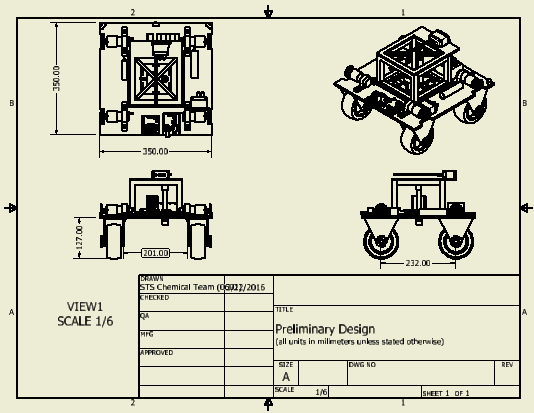
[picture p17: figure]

As seen above, these maximum dimensions permit approximately 11mm of clearance making navigation the largest issue in the design currently. With a varying sand depth (15-60mm) and pool rim height of 75mm it is expended that we must clear a height between 15-60mm. The OSV chassis is placed 127mm above the sand to provided additional room for error and any parts that may be included in later designs.

- Main Vehicle Chassis: Is constructed by one piece of sanded plywood with a thickness of 5/16 inches. From a precut size of 350x350mm, needed are made into the wood.
- Mission Specific, Syringes: To complete the advanced mission objectives two syringes are used. One (smaller) syringe is operated by a solenoid and springs to withdraw 12mL of water while one (larger) syringe, attached to a vex motor, is used to dispense a base solution. These syringes, as seen in the configurations are located on the main chassis. Plastic tubing connects these syringes to the lifting platform.
- Mission Specific, Lifting Platform: This platform contains a pH monitor, agitation pump, and needed syringe tubing and must be balanced to operate. The dimensions of this platform is 92.8x92.8x10mm to allow for a 75% error in navigating into the pool. Because this platform is suspended, it must have a balanced center of gravity. To accommodate error in balance counterweight slot are added. This calculation was made as follows.
  - Assumptions:
    - PH monitor mass=20g
    - Pump mass=50g
    - PH monitor is C of G located 28.15mm from the lifting platform center.
    - ThePH monitor and pump will be placed along a single axis.

Axis of moment

Calculation: Mph monitor +MPump =0 => (28.15mm)(20g)(9.8m/s²) = (Xm)(50g)(9.8m/s²) =>

X= -11.62mm

- Mission Specific, Lifting Chassis: To lift the platform, a box like chassis is used to guide strings, attached to a motor operated pulley, and balance the platform. This chassis consist of 7 subordinate parts as seen bellow.

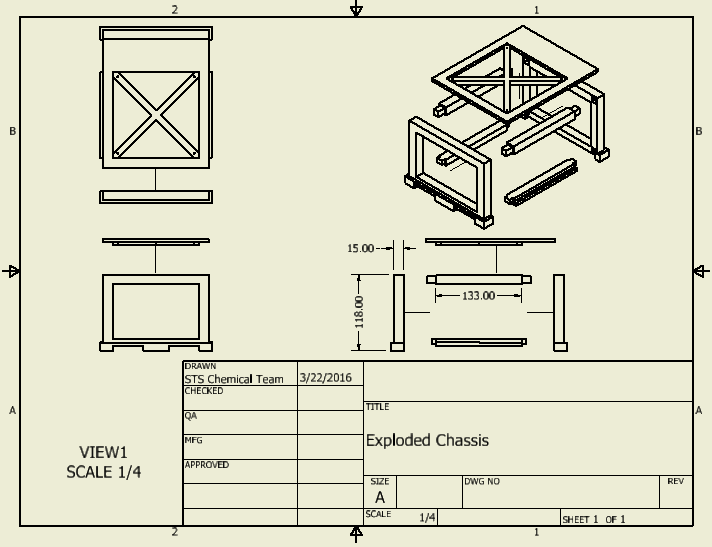
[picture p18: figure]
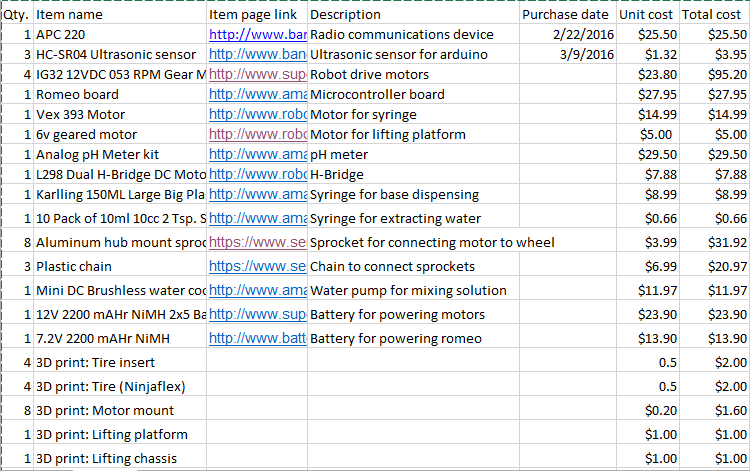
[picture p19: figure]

Bill of Materials

Current estimated total cost: $331.88

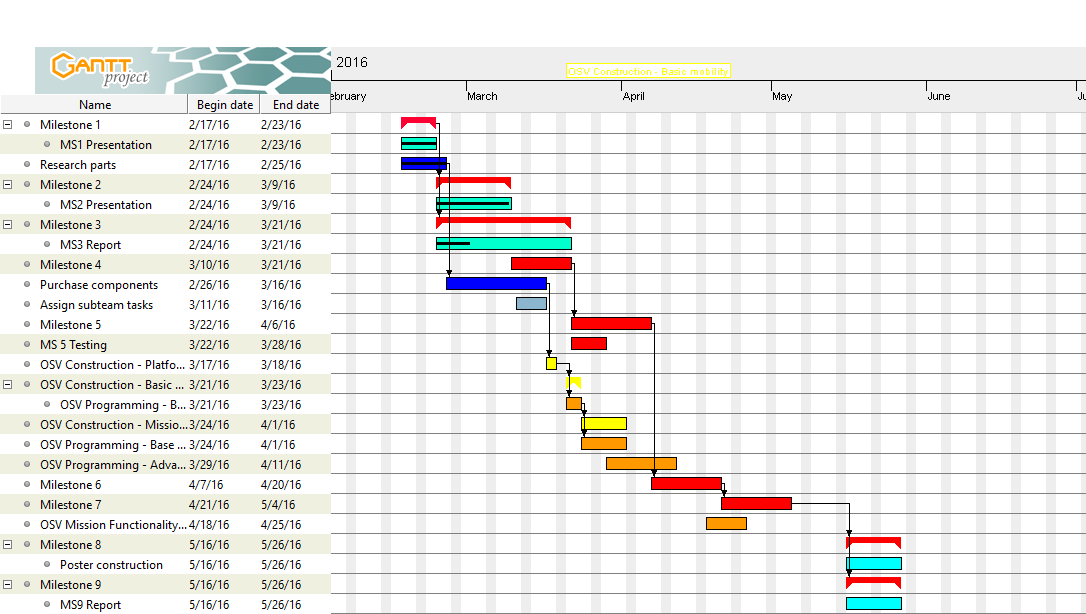
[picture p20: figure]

Gantt Chart

Construction Plan

- Begin by constructing wooden base to specifications
- Mount motors and wheels to body
  - Compsci team will work on coding for the Romeo board
- Once motors and wheels are mounted, test mobility using basic controls
- Start constructing platform with instruments
  - After platform is constructed, the platform will be tested outside of the OSV
- Start layout of secondary mission specific electronics on base body
  - This includes sensors, H-Bridge, Arduino, and batteries
- Connect the platform to the OSV and test the mechanism to drop the platform

Anticipated difficulties

- May have trouble fitting together components
  - Solution: Have CAD team work on 3d printed parts to fit everything together
- Programming can prove to be challenging
  - Solution: Dedicate more resources to development and testing of control algorithms
- Lack of time to collaborate
  - Solution: Divide up tasks so that they can be worked on individually
- Parts malfunctioning
  - Solution: Report to leader immediately so replacements can be ordered

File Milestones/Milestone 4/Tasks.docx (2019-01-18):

ENES 100

Team STS

Milestone 4

Task list

Sub teams:

Mechanical

- Isaac
- Stephen
- Kenneth

Electrical

- Eliav
- John

Computer

- Michael
- Spencer

Task list:

A. Mechanical
  - 3d printing of platform
  - 3d printing of platform support
  - Fitting together mission specific hardware onto platform
  - Developing reeling mechanism for platform and motor
  - Assembling base
  - Establish list of fittings, screws, and other minor components
B. Electrical
  - Test motors
  - Interface motors with H-bridge
  - Work with computer team to develop speed control for motors
  - Gather data on ultrasonic sensors to test operating parameters (cone, range, accuracy)
C. Computer
  - Establish a git repository for code collaboration
  - Write coding standards (indentation, comments, basic coding convention to allow for easier collaboration)
  - Brainstorm and think of methods for locomotion algorithms and methods
  - Write outlines for methods

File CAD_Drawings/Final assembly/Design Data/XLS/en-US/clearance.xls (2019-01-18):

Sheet: Ansi Unified Screw Threads
I | Sort Order -1
Fastener Type | Size | Shaft Diameters |  |  | Head Dimensions
 |  | Close | Normal | Loose | Diameter | Depth/Angle | Head Type
Flat Head Machine Screw (82) | #0 | 0.0635 | 0.07 | 0.073 | 0.119 | 82 | 2
Flat Head Machine Screw (82) | #1 | 0.076 | 0.081 | 0.089 | 0.146 | 82 | 2
Flat Head Machine Screw (82) | #2 | 0.089 | 0.096 | 0.1065 | 0.172 | 82 | 2
Flat Head Machine Screw (82) | #3 | 0.104 | 0.11 | 0.12 | 0.199 | 82 | 2
Flat Head Machine Screw (82) | #4 | 0.116 | 0.1285 | 0.136 | 0.225 | 82 | 2
Flat Head Machine Screw (82) | #5 | 0.1285 | 0.136 | 0.154 | 0.252 | 82 | 2
Flat Head Machine Screw (82) | #6 | 0.144 | 0.1495 | 0.1695 | 0.279 | 82 | 2
Flat Head Machine Screw (82) | #8 | 0.1695 | 0.177 | 0.1935 | 0.332 | 82 | 2
Flat Head Machine Screw (82) | #10 | 0.196 | 0.201 | 0.221 | 0.385 | 82 | 2
Flat Head Machine Screw (82) | #12 | 0.221 | 0.228 | 0.246 | 0.438 | 82 | 2
Flat Head Machine Screw (82) | 1/4 | 0.257 | 0.266 | 0.2812 | 0.507 | 82 | 2
Flat Head Machine Screw (82) | 5/16 | 0.323 | 0.332 | 0.3437 | 0.635 | 82 | 2
Flat Head Machine Screw (82) | 3/8 | 0.386 | 0.397 | 0.4062 | 0.762 | 82 | 2
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

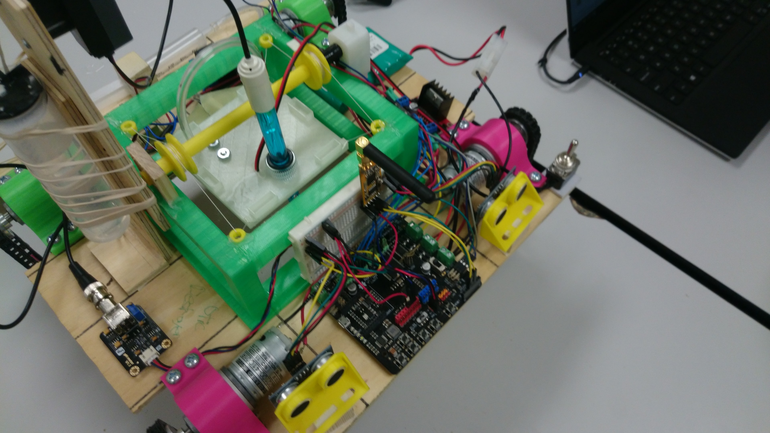
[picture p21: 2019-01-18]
Images/OSV_electronics.jpg

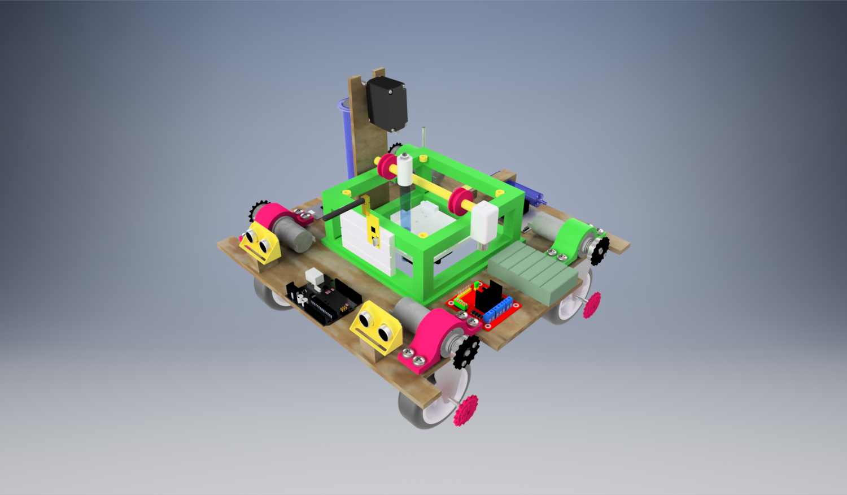
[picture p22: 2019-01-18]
Milestones/Renders/Final ortho right.png

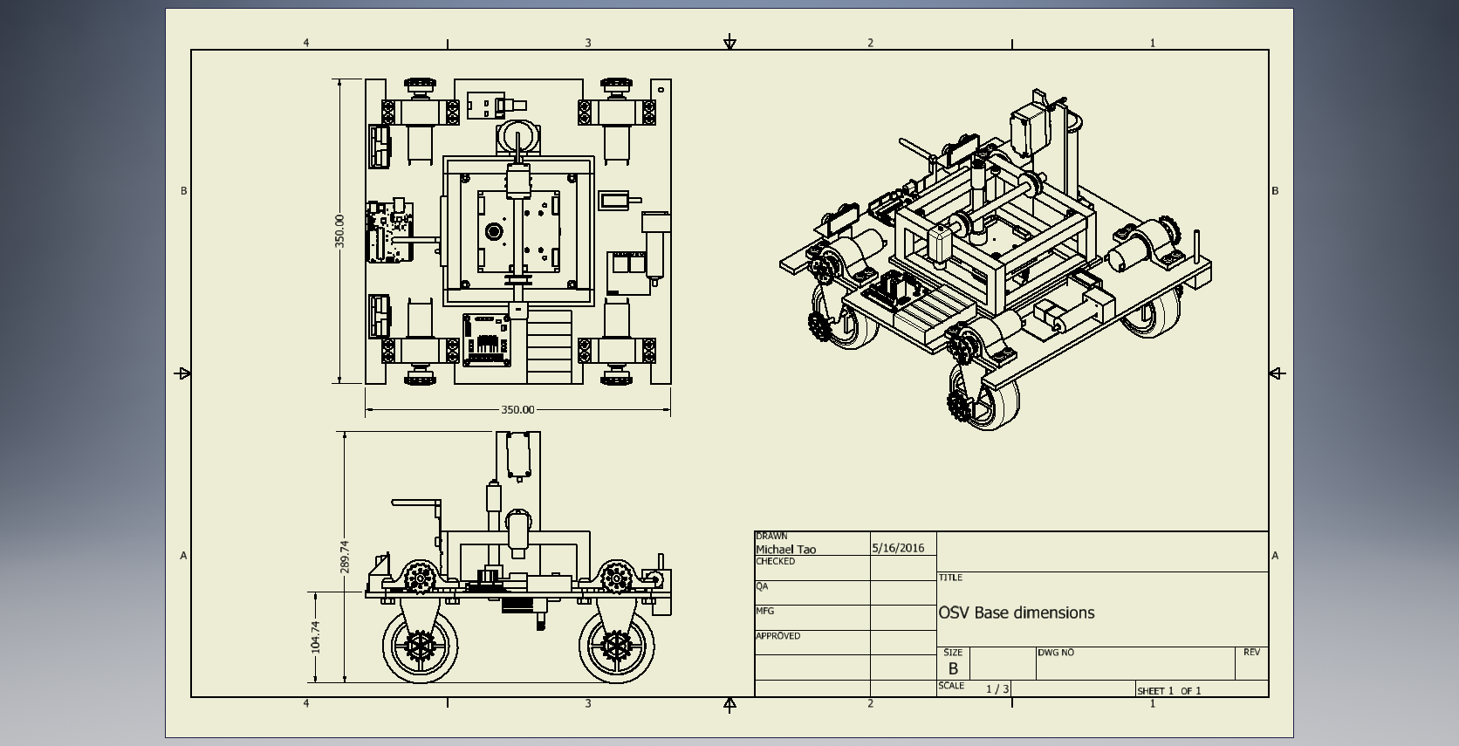
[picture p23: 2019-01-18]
Milestones/Renders/Base dimensions.png

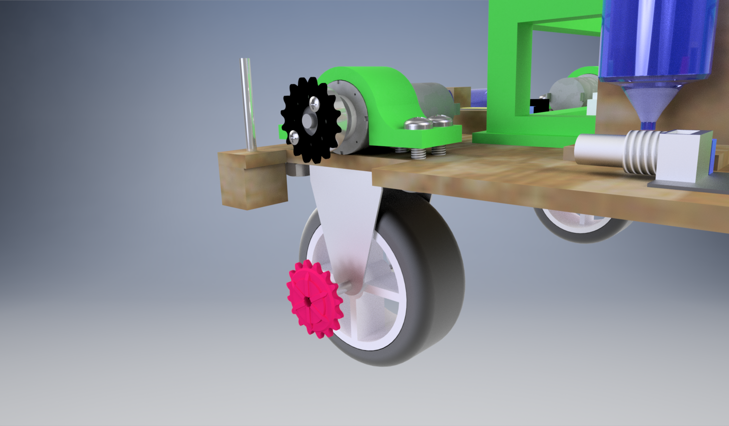
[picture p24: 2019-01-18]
Milestones/Renders/Drivechain closeup.png

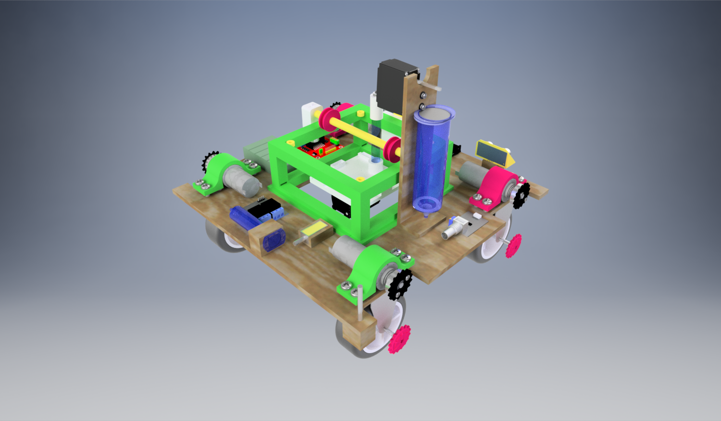
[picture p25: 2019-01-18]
Milestones/Renders/Final orgtho rear right.png

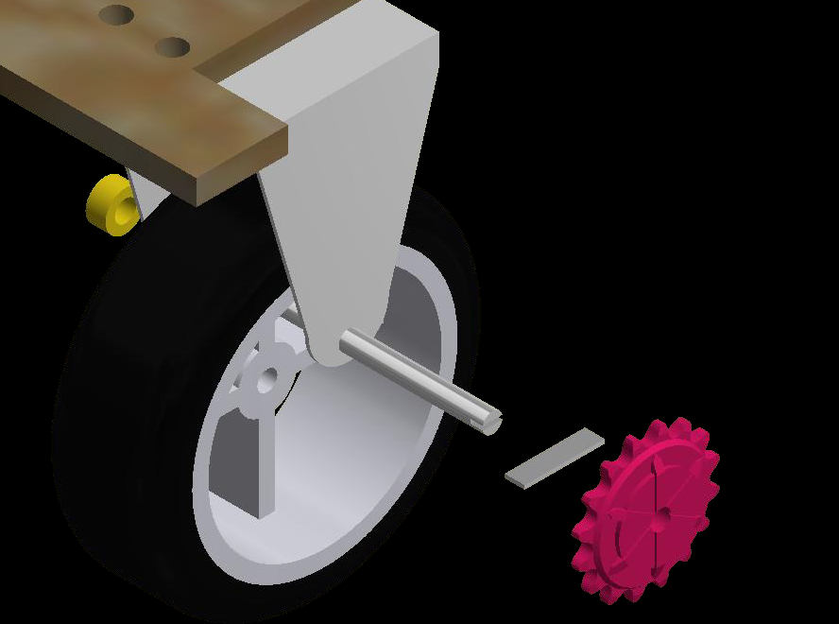
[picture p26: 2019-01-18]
Milestones/Renders/Axle sprocket connection detail.bmp

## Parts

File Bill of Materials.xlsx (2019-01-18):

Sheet: Sheet1
Qty. | Item name | Item page link | Description | Purchase date | Unit cost | Total cost | Total cost w/ shipping | Purchased by | Individual cost | Running total: | Running total w/shipping
1 | APC 220 | http://www.banggood.com/APC220-Wireless-Data-Communication-Module-USB-Adapter-Kit-For-Arduino-p-939407.html | Radio communications device | 2016-02-22 | $25.50 | $25.50 | $27.18 | Michael Tao | $3.88 | $453.36 | $519.56
5 | HC-SR04 Ultrasonic sensor | http://www.banggood.com/5Pcs-HC-SR04-Ultrasonic-Ranging-Sensor-Ultrasonic-Module-For-Arduino-p-943142.html | Ultrasonic sensor for arduino | 2016-03-09 | $1.19 | $5.95 | $7.07 | Michael Tao | $1.01 |  | $74.22
1 | Romeo board | http://www.amazon.com/gp/product/B00C9NWTQE/ref=ox_sc_mini_detail?ie=UTF8&psc=1&smid= | Microcontroller board | 2016-03-12 | $27.95 | $27.95 | $27.95 | Michael Tao | $3.99
1 | Karlling 150ML Large Big Plastic Hydroponics Nutrient Measuring Syringe | http://www.amazon.com/Karlling-Plastic-Hydroponics-Nutrient-Measuring/dp/B013DI05HI | Syringe for base dispensing | 2016-03-12 | $8.99 | $8.99 | $8.99 | Michael Tao | $1.28
1 | 10 Pack of 10ml 10cc 2 Tsp. Slip Tip Oral Medication Syringes | http://www.amazon.com/Pack-10ml-Medication-Syringes-Needle/dp/B00OABXLOM | Syringe for extracting water | 2016-03-12 | $0.66 | $0.66 | $0.66 | Michael Tao | $0.09
1 | 12v DC 600g solenoid | http://www.amazon.com/dp/B00HR8H38A/ | Solenoid for sampling syringe | 2016-03-12 | $3.46 | $3.46 | $3.46 | Michael Tao | $0.49
1 | Mini DC Brushless water cooling pump | http://www.amazon.com/ZKSJ-Brushless-Submersible-Water-cooling/dp/B00KL1JWZC/ | Water pump for mixing solution | 2016-03-12 | $11.97 | $11.97 | $11.97 | Michael Tao | $1.71
1 | Analog pH Meter kit | http://www.amazon.com/DFRobot-Analog-pH-Meter-Kit/dp/B01BNG41KO | pH meter | 2016-03-19 | $29.50 | $29.50 | $29.50 | Michael Tao | $4.21
1 | 12V 2200 mAHr NiMH 2x5 Battery Pack | http://www.superdroidrobots.com/shop/item.aspx/12v-2200-mahr-nimh-2x5-battery-pack/793/ | Battery for powering motors | 2016-03-22 | $23.90 | $23.90 | $23.90 | Michael Tao | $3.41
1 | 7.2V 2200 mAHr NiMH | http://www.batteryspace.com/Custom-NiMH-Battery-Pack-7.2V-1600-mAh-NiMH-Battery-Pack.aspx | Battery for powering romeo | 2016-03-22 | $13.90 | $13.90 | $13.90 | Michael Tao | $1.99
4 | IG32 12VDC 053 RPM Gear Motor | http://www.superdroidrobots.com/shop/item.aspx/ig32-12vdc-053-rpm-gear-motor/1165/ | Robot drive motors | 2016-03-22 | $23.80 | $95.20 | $104.10 | Michael Tao | $14.87
1 | L298 Dual H-Bridge DC Motor Controller | http://www.robotshop.com/en/l298-dual-h-bridge-dc-motor-controller.html | H-Bridge | 2016-03-22 | $7.88 | $7.88 | $7.88 | Michael Tao | $1.13
1 | KMC Z410 Bicycle Chain | http://www.amazon.com/KMC-Z410-Bicycle-1-Speed-8-Inch | Bike chain | 2016-03-29 | $9.15 | $9.15 | $9.15 | Michael Tao | $1.31
1 | 10 Pair Tamiya Big Style Connector Plugs | http://www.amazon.com/Products-Tamiya-Style-Connector-Unwired/ | Tamiya connectors | 2016-03-29 | $8.99 | $8.99 | $8.99 | Michael Tao | $1.28
1 | Tenergy Universal Smart Charger for RC | http://www.amazon.com/Tenergy-Universal-Charger-Airsoft-Battery/ | Battery charger | 2016-03-29 | $15.99 | $15.99 | $15.99 | Michael Tao | $2.28
1 | Karlling 50 ML Syringe | http://www.amazon.com/Karlling-Syringe-Nutrient-Measuring-Handy | Base dispense syringe | 2016-03-29 | $6.99 | $6.99 | $6.99 | Michael Tao | $1.00
1 | Buggy 2x Front 2x Rear Rubber Tires | http://www.amazon.com/Buggy-Rubber-Tires-RC-Off-Road/dp/B0154KEZL0?redirect=true | Tires | 2016-03-25 | $13.39 | $13.39 | $13.39 | Michael Tao | $1.91
2 | Pololu Universal Aluminum Mounting | https://www.pololu.com/product/1999 | Motor hub | 2016-04-01 | $7.95 | $15.90 | $20.85 | Michael Tao | $2.98
1 | Solarbotics GM9 143:1 Gear Motor | https://www.pololu.com/product/188 | Motor for lifting platform | 2016-04-01 | $5.95 | $5.95 | $5.95 | Michael Tao | $0.85
1 | Machine Screw: M3 | https://www.pololu.com/product/1076 | M3 Screws | 2016-04-01 | $1.29 | $1.29 | $1.29 | Michael Tao | $0.18
1 | Machine Hex Nut: M3 | https://www.pololu.com/product/1069 | M3 Nuts | 2016-04-01 | $0.99 | $0.99 | $0.99 | Michael Tao | $0.14
1 | VEX IQ Gear Kit | http://www.robotshop.com/en/vex-iq-gear-kit.html | Gears for dispensing | 2016-04-01 | $14.99 | $14.99 | $23.99 | Michael Tao | $3.43
1 | 2-Channel 5V Relay Module | http://www.robotshop.com/en/2-channel-5v-relay-module.html | Relay to switch pump if needed | 2016-04-01 | $3.15 | $3.15 | $3.15 | Michael Tao | $0.45
1 | VEX 12'' Long Square Bars (4pk) | http://www.robotshop.com/en/vex-12-long-square-bars-2pk.html | Shafts for dispensing motor | 2016-04-01 | $8.96 | $8.96 | $8.96 | Michael Tao | $1.28
1 | O1 Tool Steel Round Rod | http://www.amazon.com/Polished-Finish-Precision-Annealed-Diameter/dp/B0050RMUT2?redirect=true | Wheel axle | 2016-04-05 | $9.97 | $9.97 | $14.80 | Michael Tao | $2.11
1 | Sheet Metal | Home Depot | Metal for brackets | 2016-03-29 | $10.48 | $10.48 | $12.22 | Kenneth Daniel | $1.75
1 | Plywood | Home Depot | Base wood | 2016-03-29 | $14.35 | $14.35 | $14.35 | Kenneth Daniel | $2.05
2 | Plastic chain | https://www.servocity.com/html/plastic_chain.html#.VwbnYqQrLIU | Chain for locomotion | 2016-04-07 | $6.99 | $13.98 | $20.97 | Michael Tao | $3.00
2 | Plastic chain | https://www.servocity.com/html/plastic_chain.html#.VwbnYqQrLIU | Chain for locomotion | 2016-04-12 | $6.99 | $13.98 | $20.97 | Michael Tao | $3.00
1 | Extra Romeo board | Evandro | Replacement Romeo | 2016-04-29 | $30.00 | $30.00 | $30.00 | Isaac Lee | $4.29
1 | Poster | Mkeldin | Poster for presentation | 2016-05-15 | $20.00 | $20.00 | $20.00 | Isaac Lee | $2.86

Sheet: Sheet2
Name | Feb | Mar | April | May |  | Balance
Isaac | $20.00 | $20.00 | $8.00 | $26.22 |  | -$0.002857142857
Stephen | $20.00 | $20.00 | $20.00 | $10.00 |  | -$4.22
Spencer | $20.00 | $20.00 | $20.00 | $20.00 |  | $5.78
Kenneth | $6.00 | $40.00 | $27.00 |  |  | -$1.22
Eliav | $17.00 | $3.00 | $40.00 | $11.00 |  | -$3.22
John | $20.00 | $20.00 | $10.00 | $22.00 |  | -$2.22
Total Received | $440.22 |  |  |  | Total Balance | -$5.12
To date costs | $519.56

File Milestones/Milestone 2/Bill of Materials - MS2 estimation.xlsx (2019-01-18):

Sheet: Sheet1
Qty. | Item name | Item page link | Description | Purchase date | Unit cost | Total cost | Total cost (w/shipping) | Purchased by | Individual cost | $331.88
1 | APC 220 | http://www.banggood.com/APC220-Wireless-Data-Communication-Module-USB-Adapter-Kit-For-Arduino-p-939407.html | Radio communications device | 2016-02-22 | $25.50 | $25.50 | $27.18 | Michael Tao | $3.88
3 | HC-SR04 Ultrasonic sensor | http://www.banggood.com/5Pcs-HC-SR04-Ultrasonic-Ranging-Sensor-Ultrasonic-Module-For-Arduino-p-943142.html | Ultrasonic sensor for arduino | 2016-03-09 | $1.32 | $3.95 | $3.95 | Michael Tao | $0.56
4 | IG32 12VDC 053 RPM Gear Motor | http://www.superdroidrobots.com/shop/item.aspx/ig32-12vdc-053-rpm-gear-motor/1165/ | Robot drive motors |  | $23.80 | $95.20 | $95.20 |  | $13.60
1 | Romeo board | http://www.amazon.com/gp/product/B00C9NWTQE/ref=ox_sc_mini_detail?ie=UTF8&psc=1&smid= | Microcontroller board |  | $27.95 | $27.95 | $27.95 |  | $3.99
1 | Vex 393 Motor | http://www.robotshop.com/en/100-rpm-vex-2-wire-motor-393.html | Motor for syringe |  | $14.99 | $14.99 | $14.99 |  | $2.14
1 | 6v geared motor | http://www.robotshop.com/en/dfrobot-6v-180-rpm-micro-dc-geared-motor-with-back-shaft.html | Motor for lifting platform |  | $5.00 | $5.00 | $5.00 |  | $0.71
1 | Analog pH Meter kit | http://www.amazon.com/DFRobot-Analog-pH-Meter-Kit/dp/B01BNG41KO | pH meter |  | $29.50 | $29.50 | $29.50 |  | $4.21
1 | L298 Dual H-Bridge DC Motor Controller | http://www.robotshop.com/en/l298-dual-h-bridge-dc-motor-controller.html | H-Bridge |  | $7.88 | $7.88 | $7.88 |  | $1.13
1 | Karlling 150ML Large Big Plastic Hydroponics Nutrient Measuring Syringe | http://www.amazon.com/Karlling-Plastic-Hydroponics-Nutrient-Measuring/dp/B013DI05HI | Syringe for base dispensing |  | $8.99 | $8.99 | $8.99 |  | $1.28
1 | 10 Pack of 10ml 10cc 2 Tsp. Slip Tip Oral Medication Syringes | http://www.amazon.com/Pack-10ml-Medication-Syringes-Needle/dp/B00OABXLOM | Syringe for extracting water |  | $0.66 | $0.66 | $0.66 |  | $0.09
8 | Aluminum hub mount sprocket | https://www.servocity.com/html/aluminum_hub_mount_sprockets__.html#.VuEgvpwrLIW | Sprocket for connecting motor to wheel |  | $3.99 | $31.92 | $31.92 |  | $4.56
3 | Plastic chain | https://www.servocity.com/html/plastic_chain.html#.VuEhBJwrLIU | Chain to connect sprockets |  | $6.99 | $20.97 | $20.97 |  | $3.00
1 | Mini DC Brushless water cooling pump | http://www.amazon.com/ZKSJ-Brushless-Submersible-Water-cooling/dp/B00KL1JWZC/ | Water pump for mixing solution |  | $11.97 | $11.97 | $11.97 |  | $1.71
1 | 12V 2200 mAHr NiMH 2x5 Battery Pack | http://www.superdroidrobots.com/shop/item.aspx/12v-2200-mahr-nimh-2x5-battery-pack/793/ | Battery for powering motors |  | $23.90 | $23.90 | $23.90 |  | $3.41
1 | 7.2V 2200 mAHr NiMH | http://www.batteryspace.com/Custom-NiMH-Battery-Pack-7.2V-1600-mAh-NiMH-Battery-Pack.aspx | Battery for powering romeo |  | $13.90 | $13.90 | $13.90 |  | $1.99
4 | 3D print: Tire insert |  |  |  | 0.5 | $2.00 | 2 |  | 0.2857142857
4 | 3D print: Tire (Ninjaflex) |  |  |  | 0.5 | $2.00 | 2 |  | 0.2857142857
8 | 3D print: Motor mount |  |  |  | $0.20 | $1.60 | $1.60 |  | $0.23
1 | 3D print: Lifting platform |  |  |  | $1.00 | $1.00 | 1 |  | $0.14
1 | 3D print: Lifting chassis |  |  |  | $1.00 | $1.00 | 1 |  | $0.14
4 | 3D print: Wheel mount |  |  |  | $0.50 | $2.00 | 2 |  | $0.29

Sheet: Sheet2
Name | Feb |  | Balance
Isaac | $20.00 |  | -$24.29
Stephen | $20.00 |  | -$24.29
Spencer | $20.00 |  | -$24.29
Kenneth | $6.00 |  | -$38.29
Eliav | $17.00 |  | -$27.29
John | $20.00 |  | -$24.29
Total Received | $103.00 | Total Bal | -$162.77
To date costs | $310.06

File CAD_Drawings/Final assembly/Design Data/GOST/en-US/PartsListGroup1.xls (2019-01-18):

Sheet: Лист 1
Инв. № подл |  |  |  | Подп. и дата | Взам. инв. № | Инв. № дубл. |  |  | Подп. и дата
Формат | Зона | Поз. | Обозначение |  |  |  | Наименование |  |  |  |  |  | Кол. на исполнение
 |  |  |  |  |  |  |  |  |  |  |  | Лит.
 |  |  |  |  |  |  |  |  |  |  |  | Код
 |  |  |  |  |  |  |  | Изм. | Лист | № докум | Подпись |  | Дата
 |  |  |  |  |  |  |  | Разраб.
 |  |  |  |  |  |  |  | Пров.
 |  |  |  |  |  |  |  | Н.контр
 |  |  |  |  |  |  |  | Утв.
 |  |  |  |  |  |  |  |  |  |  |  |  |  | Копировал

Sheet: Лист 2
Инв. № подл |  |  |  | Подп. и дата | Взам. инв. № | Инв. № дубл. |  |  | Подп. и дата
Формат | Зона | Поз. | Обозначение |  |  |  | Наименование |  |  |  |  | Кол. на исполнение
 |  |  |  |  |  |  |  | Изм. | Лист | № докум. | Подп. | Дата
 |  |  |  |  |  |  |  |  |  |  |  |  | Копировал
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

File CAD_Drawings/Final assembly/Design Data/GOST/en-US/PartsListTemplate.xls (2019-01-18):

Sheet: Лист 1
 | Формат | Зона |  | Поз. |  | Обозначение |  |  |  | Наименование |  |  |  | Кол. | Приме-чание
Подп. и дата
Инв. № дубл.
Взам. инв. №
Подп. и дата
 | Изм. |  | Лист |  | № докум |  | Подпись | Дата
Инв. № подл | Разраб. |  |  |  |  |  |  |  |  |  | Литера |  | Лист |  |  | Листов
 | Пров.
 | Н.контр
 | Утв.
 |  |  |  |  |  |  |  |  | Копировал |  |  | Формат А4

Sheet: Лист 2
 | Формат | Зона |  | Поз. |  | Обозначение |  |  |  | Наименование |  | Кол. | Приме-чание
Подп. и дата
Инв. № дубл.
Взам. инв. №
Подп. и дата
Инв. № подл
 | Изм. |  | Лист |  | № докум. |  | Подп. |  | Дата
 |  |  |  |  |  |  |  | Копировал |  |  | Формат А4
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

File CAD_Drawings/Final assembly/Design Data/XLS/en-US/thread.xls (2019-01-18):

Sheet: Inch Tapping Threads
I Q X | Inch Tapping Threads |  | Sort Order - 5 |  | External |  |  |  |  |  |  | Internal
 |  |  |  |  |  | Major Dia |  | Pitch Dia |  | Minor Dia |  |  | Minor Dia |  | Pitch Dia |  | Major Dia |  | Tap Drill
Size | Size Suffix | Thread Designation | Custom Thread Designation | TPI | Class | Max | Min | Max | Min | Max | Min | Class | Min | Max | Min | Max | Min | Max | Basic
0.0600 |  | 0-48 | 0-48 | 48 | 2B | 0.0600 | 0.0540 | 0.0480 | 0.0435 | 0.0360 | 0.0330
0.0730 |  | 1-42 | 1-42 | 42 | 2B | 0.0750 | 0.0690 | 0.0620 | 0.0575 | 0.0490 | 0.0460
0.0860 |  | 2-32 | 2-32 | 32 | 2B | 0.0880 | 0.0820 | 0.0760 | 0.0710 | 0.0640 | 0.0600
0.0990 |  | 3-28 | 3-28 | 28 | 2B | 0.1010 | 0.0950 | 0.0880 | 0.0830 | 0.0750 | 0.0710
0.1120 |  | 4-24 | 4-24 | 24 | 2B | 0.1140 | 0.1080 | 0.1000 | 0.0950 | 0.0860 | 0.0820
0.1250 |  | 5-20 | 5-20 | 20 | 2B | 0.1300 | 0.1230 | 0.1120 | 0.1065 | 0.0940 | 0.0900
0.1380 |  | 6-20 | 6-20 | 20 | 2B | 0.1390 | 0.1320 | 0.1215 | 0.1155 | 0.1040 | 0.0990
0.1510 |  | 7-19 | 7-19 | 19 | 2B | 0.1540 | 0.1470 | 0.1345 | 0.1280 | 0.1150 | 0.1090
0.1640 |  | 8-18 | 8-18 | 18 | 2B | 0.1660 | 0.1590 | 0.1440 | 0.1375 | 0.1220 | 0.1160
0.1900 |  | 10-16 | 10-16 | 16 | 2B | 0.1890 | 0.1820 | 0.1650 | 0.1585 | 0.1410 | 0.1350
0.2160 |  | 12-14 | 12-14 | 14 | 2B | 0.2150 | 0.2080 | 0.1895 | 0.1825 | 0.1640 | 0.1570
0.2420 |  | 14-14 | 14-14 | 14 | 2B | 0.2410 | 0.2340 | 0.2130 | 0.2060 | 0.1850 | 0.1780
0.2500 |  | 1/4-14 | 1/4-14 | 14 | 2B | 0.2460 | 0.2370 | 0.2190 | 0.2110 | 0.1920 | 0.1850
0.3125 |  | 5/16-12 | 5/16-12 | 12 | 2B | 0.3150 | 0.3060 | 0.2795 | 0.2710 | 0.2440 | 0.2360
0.3750 |  | 3/8-12 | 3/8-12 | 12 | 2B | 0.3800 | 0.3710 | 0.3445 | 0.3350 | 0.3090 | 0.2990
0.4375 |  | 7/16-10 | 7/16-10 | 10 | 2B | 0.4400 | 0.4290 | 0.3995 | 0.3890 | 0.3590 | 0.3490
0.5000 |  | 1/2-10 | 1/2-10 | 10 | 2B | 0.5040 | 0.4930 | 0.4635 | 0.4530 | 0.4230 | 0.4130

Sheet: Metric Forming Screw Threads
M P X | Metric Forming Screw Threads |  | Sort Order - 6 |  | External |  |  |  |  |  |  | Internal
 |  |  |  |  |  | Major Dia |  | Pitch Dia |  | Minor Dia |  |  | Minor Dia |  | Pitch Dia |  | Major Dia |  | Tap Drill
Size | Size Suffix | Thread Designation | Custom Thread Designation | Pitch | Class | Max | Min | Max | Min | Max | Min | Class | Min | Max | Min | Max | Min | Max | Basic
1.5 |  | 1.5x0.5 | 1.5x0.5 | 0.5 | 6g | 1.520 | 1.380 | 1.215 | 1.110 | 0.910 | 0.840
1.5 |  | ST1.5x0.5 | ST1.5x0.5 | 0.5 | 6g | 1.520 | 1.380 | 1.215 | 1.110 | 0.910 | 0.840
1.9 |  | 1.9x0.6 | 1.9x0.6 | 0.6 | 6g | 1.900 | 1.760 | 1.570 | 1.465 | 1.240 | 1.170
1.9 |  | ST1.9x0.6 | ST1.9x0.6 | 0.6 | 6g | 1.900 | 1.760 | 1.570 | 1.465 | 1.240 | 1.170
2.2 |  | 2.2x0.8 | 2.2x0.8 | 0.8 | 6g | 2.240 | 2.100 | 1.935 | 1.810 | 1.630 | 1.520
2.2 |  | ST2.2x0.8 | ST2.2x0.8 | 0.8 | 6g | 2.240 | 2.100 | 1.935 | 1.810 | 1.630 | 1.520
2.6 |  | 2.6x0.9 | 2.6x0.9 | 0.9 | 6g | 2.570 | 2.430 | 2.235 | 2.115 | 1.900 | 1.800
2.6 |  | ST2.6x0.9 | ST2.6x0.9 | 0.9 | 6g | 2.570 | 2.430 | 2.235 | 2.115 | 1.900 | 1.800
2.9 |  | 2.9x1 | 2.9x1 | 1 | 6g | 2.900 | 2.760 | 2.540 | 2.420 | 2.180 | 2.080
2.9 |  | 2.9x1.1 | 2.9x1.1 | 1.1 | 6g | 2.900 | 2.760 | 2.540 | 2.420 | 2.180 | 2.080
2.9 |  | ST2.9x1.1 | ST2.9x1.1 | 1.1 | 6g | 2.900 | 2.760 | 2.540 | 2.420 | 2.180 | 2.080
2.9 |  | 2.9x1.3 | 2.9x1.3 | 1.3 | 6g | 2.900 | 2.720 | 2.540 | 2.355 | 1.890 | 1.700
2.9 |  | 2.9x1.4 | 2.9x1.4 | 1.4 | 6g | 2.900 | 2.720 | 2.340 | 2.175 | 1.780 | 1.630
3.3 |  | 3.3x1.3 | 3.3x1.3 | 1.3 | 6g | 3.300 | 3.120 | 2.795 | 2.665 | 2.290 | 2.210
3.3 |  | ST3.3x1.3 | ST3.3x1.3 | 1.3 | 6g | 3.300 | 3.120 | 2.795 | 2.665 | 2.290 | 2.210
3.5 |  | 3.5x1.3 | 3.5x1.3 | 1.3 | 6g | 3.530 | 3.350 | 3.085 | 2.930 | 2.640 | 2.510
3.5 |  | ST3.5x1.3 | ST3.5x1.3 | 1.3 | 6g | 3.530 | 3.350 | 3.085 | 2.930 | 2.640 | 2.510
3.5 |  | 3.5x1.6 | 3.5x1.6 | 1.6 | 6g | 3.530 | 3.350 | 2.920 | 2.755 | 2.310 | 2.160
3.5 |  | 3.5x3.2 | 3.5x3.2 | 3.2 | 6g | 3.530 | 3.310 | 2.800 | 2.600 | 2.070 | 1.890
3.9 |  | 3.9x1.3 | 3.9x1.3 | 1.3 | 6g | 3.910 | 3.730 | 3.415 | 3.250 | 2.920 | 2.770
3.9 |  | ST3.9x1.3 | ST3.9x1.3 | 1.3 | 6g | 3.910 | 3.730 | 3.415 | 3.250 | 2.920 | 2.770
3.9 |  | 3.9x1.6 | 3.9x1.6 | 1.6 | 6g | 3.910 | 3.730 | 3.300 | 3.135 | 2.690 | 2.540
3.9 |  | 3.9x3.2 | 3.9x3.2 | 3.2 | 6g | 3.910 | 3.690 | 3.180 | 2.980 | 2.450 | 2.270
4.2 |  | 4.2x1.4 | 4.2x1.4 | 1.4 | 6g | 4.220 | 4.040 | 3.660 | 3.495 | 3.100 | 2.950
4.2 |  | ST4.2x1.4 | ST4.2x1.4 | 1.4 | 6g | 4.220 | 4.040 | 3.660 | 3.495 | 3.100 | 2.950
4.2 |  | 4.2x1.6 | 4.2x1.6 | 1.6 | 6g | 4.220 | 4.040 | 3.610 | 3.445 | 3.000 | 2.850
4.2 |  | 4.2x3.2 | 4.2x3.2 | 3.2 | 6g | 4.220 | 4.000 | 3.380 | 3.180 | 2.540 | 2.360
4.8 |  | 4.8x1.6 | 4.8x1.6 | 1.6 | 6g | 4.800 | 4.620 | 4.190 | 4.025 | 3.580 | 3.430
4.8 |  | ST4.8x1.6 | ST4.8x1.6 | 1.6 | 6g | 4.800 | 4.620 | 4.190 | 4.025 | 3.580 | 3.430
4.8 |  | 4.8x1.8 | 4.8x1.8 | 1.8 | 6g | 4.800 | 4.620 | 4.065 | 3.885 | 3.330 | 3.150
4.8 |  | 4.8x3.2 | 4.8x3.2 | 3.2 | 6g | 4.800 | 4.580 | 3.960 | 3.760 | 3.120 | 2.940
5.5 |  | 5.5x1.8 | 5.5x1.8 | 1.8 | 6g | 5.460 | 5.280 | 4.815 | 4.635 | 4.170 | 3.990
5.5 |  | ST5.5x1.8 | ST5.5x1.8 | 1.8 | 6g | 5.460 | 5.280 | 4.815 | 4.635 | 4.170 | 3.990
6.3 |  | 6.3x1.8 | 6.3x1.8 | 1.8 | 6g | 6.250 | 6.030 | 5.565 | 5.365 | 4.880 | 4.700
6.3 |  | ST6.3x1.8 | ST6.3x1.8 | 1.8 | 6g | 6.250 | 6.030 | 5.565 | 5.365 | 4.880 | 4.700
8.0 |  | 8x2.1 | 8x2.1 | 2.1 | 6g | 8.000 | 7.780 | 7.100 | 6.885 | 6.200 | 5.990
8.0 |  | ST8x2.1 | ST8x2.1 | 2.1 | 6g | 8.000 | 7.780 | 7.100 | 6.885 | 6.200 | 5.990
9.5 |  | 9.5x2.1 | 9.5x2.1 | 2.1 | 6g | 9.650 | 9.430 | 8.750 | 8.510 | 7.850 | 7.590
9.5 |  | ST9.5x2.1 | ST9.5x2.1 | 2.1 | 6g | 9.650 | 9.430 | 8.750 | 8.510 | 7.850 | 7.590

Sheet: ISO Pipe Threads
M Q | ISO Pipe Threads |  | Sort Order - 9 |  | External |  |  |  |  |  |  | Internal
 |  |  |  |  |  | Major Dia |  | Pitch Dia |  | Minor Dia |  |  | Minor Dia |  | Pitch Dia |  | Major Dia |  | Tap Drill | Thread Depth | Thread Runouts
Size | Size Suffix | Thread Designation | Custom Thread Designation | TPI | Class | Max | Min | Max | Min | Max | Min | Class | Min | Max | Min | Max | Min | Max | Basic
7.723 |  | G7.723x0.907 | G 1/16 | 28 | A | 7.723 | 7.509 | 7.142 | 7.035 | 6.561 |  |  | 6.561 | 6.834 | 7.142 | 7.249 | 7.723 |  | 1.5875 | 15.446 | 4.5000
7.723 |  | G7.723x0.907 | G 1/16 | 28 | B | 7.723 | 7.509 | 7.142 | 6.928 | 6.561
9.728 |  | G9.728x0.907 | G 1/8 | 28 | A | 9.728 | 9.514 | 9.147 | 9.040 | 8.566 |  |  | 8.566 | 8.848 | 9.147 | 9.254 | 9.728 |  | 3.1750 | 19.456 | 4.5000
9.728 |  | G9.728x0.907 | G 1/8 | 28 | B | 9.728 | 9.514 | 9.147 | 8.933 | 8.566
13.157 |  | G13.157x1.337 | G 1/4 | 19 | A | 13.157 | 12.907 | 12.301 | 12.176 | 11.445 |  |  | 11.445 | 11.89 | 12.301 | 12.426 | 13.157 |  | 6.3500 | 26.314 | 6.5000
13.157 |  | G13.157x1.337 | G 1/4 | 19 | B | 13.157 | 12.907 | 12.301 | 12.051 | 11.445
16.662 |  | G16.662x1.337 | G 3/8 | 19 | A | 16.662 | 16.412 | 15.806 | 15.681 | 14.950 |  |  | 14.95 | 15.395 | 15.806 | 15.931 | 16.662 |  | 9.5250 | 33.324 | 6.5000
16.662 |  | G16.662x1.337 | G 3/8 | 19 | B | 16.662 | 16.412 | 15.806 | 15.556 | 14.950
20.955 |  | G20.955x1.814 | G 1/2 | 14 | A | 20.955 | 20.671 | 19.793 | 19.651 | 18.631 |  |  | 18.631 | 19.172 | 19.793 | 19.935 | 20.955 |  | 12.7000 | 41.910 | 8.5000
20.955 |  | G20.955x1.814 | G 1/2 | 14 | B | 20.955 | 20.671 | 19.793 | 19.509 | 18.631
22.911 |  | G22.911x1.814 | G 5/8 | 14 | A | 22.911 | 22.627 | 21.749 | 21.607 | 20.587 |  |  | 20.587 | 21.128 | 21.749 | 21.891 | 22.911 |  |  | 45.822 | 8.5000
22.911 |  | G22.911x1.814 | G 5/8 | 14 | B | 22.911 | 22.627 | 21.749 | 21.465 | 20.587
26.441 |  | G26.441x1.814 | G 3/4 | 14 | A | 26.441 | 26.157 | 25.279 | 25.137 | 24.117 |  |  | 24.117 | 24.658 | 25.279 | 25.421 | 26.441 |  | 15.8750 | 52.882 | 8.5000
26.441 |  | G26.441x1.814 | G 3/4 | 14 | B | 26.441 | 26.157 | 25.279 | 24.995 | 24.117
30.201 |  | G30.201x1.814 | G 7/8 | 14 | A | 30.201 | 29.917 | 29.039 | 28.897 | 27.877 |  |  | 27.877 | 28.418 | 29.039 | 29.181 | 30.201 |  | 22.2250 | 60.402 | 8.5000
30.201 |  | G30.201x1.814 | G 7/8 | 14 | B | 30.201 | 29.917 | 29.039 | 28.755 | 27.877
33.249 |  | G33.249x2.309 | G 1 | 11 | A | 33.249 | 32.889 | 31.770 | 31.590 | 30.291 |  |  | 30.291 | 30.931 | 31.77 | 31.95 | 33.249 |  | 25.4000 | 66.498 | 10.0000
33.249 |  | G33.249x2.309 | G 1 | 11 | B | 33.249 | 32.889 | 31.770 | 31.410 | 30.291
37.897 |  | G37.897x2.309 | G 1 1/8 | 11 | A | 37.897 | 37.537 | 36.418 | 36.238 | 34.939 |  |  | 34.939 | 35.579 | 36.418 | 36.598 | 37.897 |  | 28.5750 | 75.794 | 10.0000
37.897 |  | G37.897x2.309 | G 1 1/8 | 11 | B | 37.897 | 37.537 | 36.418 | 36.058 | 34.939
41.910 |  | G41.91x2.309 | G 1 1/4 | 11 | A | 41.910 | 41.550 | 40.431 | 40.251 | 38.952 |  |  | 38.952 | 39.592 | 40.431 | 40.611 | 41.910 |  | 31.7500 | 83.820 | 10.0000
41.910 |  | G41.91x2.309 | G 1 1/4 | 11 | B | 41.910 | 41.550 | 40.431 | 40.071 | 38.952
47.803 |  | G47.803x2.309 | G 1 1/2 | 11 | A | 47.803 | 47.443 | 46.324 | 46.144 | 44.845 |  |  | 44.845 | 45.485 | 46.324 | 46.504 | 47.803 |  | 38.1000 | 95.606 | 10.0000
47.803 |  | G47.803x2.309 | G 1 1/2 | 11 | B | 47.803 | 47.443 | 46.324 | 45.964 | 44.845
53.746 |  | G53.746x2.309 | G 1 3/4 | 11 | A | 53.746 | 53.386 | 52.267 | 52.087 | 50.788 |  |  | 50.788 | 51.428 | 52.267 | 52.447 | 53.746 |  | 44.4500 | 107.492 | 10.0000
53.746 |  | G53.746x2.309 | G 1 3/4 | 11 | B | 53.746 | 53.386 | 52.267 | 51.907 | 50.788
59.614 |  | G59.614x2.309 | G 2 | 11 | A | 59.614 | 59.254 | 58.135 | 57.955 | 56.656 |  |  | 56.656 | 57.296 | 58.135 | 58.315 | 59.614 |  | 50.8000 | 119.228 | 10.0000
59.614 |  | G59.614x2.309 | G 2 | 11 | B | 59.614 | 59.254 | 58.135 | 57.775 | 56.656
65.710 |  | G65.71x2.309 | G 2 1/4 | 11 | A | 65.710 | 65.276 | 64.231 | 64.014 | 62.752 |  |  | 62.752 | 63.392 | 64.231 | 64.448 | 65.710 |  | 57.1500 | 131.420 | 10.0000
65.710 |  | G65.71x2.309 | G 2 1/4 | 11 | B | 65.710 | 65.276 | 64.231 | 63.797 | 62.752
75.184 |  | G75.184x2.309 | G 2 1/2 | 11 | A | 75.184 | 74.750 | 73.705 | 73.488 | 72.226 |  |  | 72.226 | 72.866 | 73.705 | 73.922 | 75.184 |  |  | 150.368 | 10.0000
75.184 |  | G75.184x2.309 | G 2 1/2 | 11 | B | 75.184 | 74.750 | 73.705 | 73.271 | 72.226
81.534 |  | G81.534x2.309 | G 2 3/4 | 11 | A | 81.534 | 81.100 | 80.055 | 79.838 | 78.576 |  |  | 78.576 | 79.216 | 80.055 | 80.272 | 81.534 |  | 69.8500 | 163.068 | 10.0000
81.534 |  | G81.534x2.309 | G 2 3/4 | 11 | B | 81.534 | 81.100 | 80.055 | 79.621 | 78.576
87.884 |  | G87.884x2.309 | G 3 | 11 | A | 87.884 | 87.450 | 86.405 | 86.188 | 84.926 |  |  | 84.926 | 85.566 | 86.405 | 86.622 | 87.884 |  | 76.2000 | 175.768 | 10.0000
87.884 |  | G87.884x2.309 | G 3 | 11 | B | 87.884 | 87.450 | 86.405 | 85.971 | 84.926
100.330 |  | G100.33x2.309 | G 3 1/2 | 11 | A | 100.330 | 99.896 | 98.851 | 98.634 | 97.372 |  |  | 97.372 | 98.012 | 98.851 | 99.068 | 100.330 |  | 88.9000 | 200.660 | 10.0000
100.330 |  | G100.33x2.309 | G 3 1/2 | 11 | B | 100.330 | 99.896 | 98.851 | 98.417 | 97.372
113.030 |  | G113.03x2.309 | G 4 | 11 | A | 113.030 | 112.596 | 111.551 | 111.334 | 110.072 |  |  | 110.072 | 110.712 | 111.551 | 111.768 | 113.030 |  | 101.6000 | 226.060 | 10.0000
113.030 |  | G113.03x2.309 | G 4 | 11 | B | 113.030 | 112.596 | 111.551 | 111.117 | 110.072
125.730 |  | G125.73x2.309 | G 4 1/2 | 11 | A | 125.730 | 125.296 | 124.251 | 124.034 | 122.772 |  |  | 122.772 | 123.412 | 124.251 | 124.468 | 125.730 |  | 114.3000 | 251.460 | 10.0000
125.730 |  | G125.73x2.309 | G 4 1/2 | 11 | B | 125.730 | 125.296 | 124.251 | 123.817 | 122.772
138.430 |  | G138.43x2.309 | G 5 | 11 | A | 138.430 | 137.996 | 136.951 | 136.734 | 135.472 |  |  | 135.472 | 136.112 | 136.951 | 137.168 | 138.430 |  | 127.0000 | 276.860 | 10.0000
138.430 |  | G138.43x2.309 | G 5 | 11 | B | 138.430 | 137.996 | 136.951 | 136.517 | 135.472
151.130 |  | G151.13x2.309 | G 5 1/2 | 11 | A | 151.130 | 150.696 | 149.651 | 149.434 | 148.172 |  |  | 148.172 | 148.812 | 149.651 | 149.868 | 151.130 |  | 139.7000 | 302.260 | 10.0000
151.130 |  | G151.13x2.309 | G 5 1/2 | 11 | B | 151.130 | 150.696 | 149.651 | 149.217 | 148.172
163.830 |  | G163.83x2.309 | G 6 | 11 | A | 163.830 | 163.396 | 162.351 | 162.134 | 160.872 |  |  | 160.872 | 161.512 | 162.351 | 162.568 | 163.830 |  | 152.4000 | 327.660 | 10.0000
163.830 |  | G163.83x2.309 | G 6 | 11 | B | 163.830 | 163.396 | 162.351 | 161.917 | 160.872

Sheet: JIS Pipe Threads
M Q | JIS Pipe Threads |  | Sort Order -12 |  | External |  |  |  |  |  |  | Internal
 |  |  |  |  |  | Major Dia |  | Pitch Dia |  | Minor Dia |  |  | Minor Dia |  | Pitch Dia |  | Major Dia |  | Tap Drill | Thread Depth | Thread Runouts
Size | Size Suffix | Thread Designation | Custom Thread Designation | TPI | Class | Max | Min | Max | Min | Max | Min | Class | Min | Max | Min | Max | Min | Max | Basic |  | Basic
7.723 |  | G7.723x0.907 | G 1/16 | 28 | A | 7.723 | 7.509 | 7.142 | 7.035 | 6.561 |  |  | 6.561 | 6.834 | 7.142 | 7.249 | 7.723 |  | 1.5875 | 15.446 | 4.5000
7.723 |  | G7.723x0.907 | G 1/16 | 28 | B | 7.723 | 7.509 | 7.142 | 6.928 | 6.561
9.728 |  | G9.728x0.907 | G 1/8 | 28 | A | 9.728 | 9.514 | 9.147 | 9.040 | 8.566 |  |  | 8.566 | 8.848 | 9.147 | 9.254 | 9.728 |  | 3.1750 | 19.456 | 4.5000
9.728 |  | G9.728x0.907 | G 1/8 | 28 | B | 9.728 | 9.514 | 9.147 | 8.933 | 8.566
13.157 |  | G13.157x1.337 | G 1/4 | 19 | A | 13.157 | 12.907 | 12.301 | 12.176 | 11.445 |  |  | 11.445 | 11.89 | 12.301 | 12.426 | 13.157 |  | 6.3500 | 26.314 | 6.5000
13.157 |  | G13.157x1.337 | G 1/4 | 19 | B | 13.157 | 12.907 | 12.301 | 12.051 | 11.445
16.662 |  | G16.662x1.337 | G 3/8 | 19 | A | 16.662 | 16.412 | 15.806 | 15.681 | 14.950 |  |  | 14.95 | 15.395 | 15.806 | 15.931 | 16.662 |  | 9.5250 | 33.324 | 6.5000
16.662 |  | G16.662x1.337 | G 3/8 | 19 | B | 16.662 | 16.412 | 15.806 | 15.556 | 14.950
20.955 |  | G20.955x1.814 | G 1/2 | 14 | A | 20.955 | 20.671 | 19.793 | 19.651 | 18.631 |  |  | 18.631 | 19.172 | 19.793 | 19.935 | 20.955 |  | 12.7000 | 41.910 | 8.5000
20.955 |  | G20.955x1.814 | G 1/2 | 14 | B | 20.955 | 20.671 | 19.793 | 19.509 | 18.631
22.911 |  | G22.911x1.814 | G 5/8 | 14 | A | 22.911 | 22.627 | 21.749 | 21.607 | 20.587 |  |  | 20.587 | 21.128 | 21.749 | 21.891 | 22.911 |  |  | 45.822 | 8.5000
22.911 |  | G22.911x1.814 | G 5/8 | 14 | B | 22.911 | 22.627 | 21.749 | 21.465 | 20.587
26.441 |  | G26.441x1.814 | G 3/4 | 14 | A | 26.441 | 26.157 | 25.279 | 25.137 | 24.117 |  |  | 24.117 | 24.658 | 25.279 | 25.421 | 26.441 |  | 15.8750 | 52.882 | 8.5000
26.441 |  | G26.441x1.814 | G 3/4 | 14 | B | 26.441 | 26.157 | 25.279 | 24.995 | 24.117
30.201 |  | G30.201x1.814 | G 7/8 | 14 | A | 30.201 | 29.917 | 29.039 | 28.897 | 27.877 |  |  | 27.877 | 28.418 | 29.039 | 29.181 | 30.201 |  | 22.2250 | 60.402 | 8.8000
30.201 |  | G30.201x1.814 | G 7/8 | 14 | B | 30.201 | 29.917 | 29.039 | 28.755 | 27.877
33.249 |  | G33.249x2.309 | G 1 | 11 | A | 33.249 | 32.889 | 31.770 | 31.590 | 30.291 |  |  | 30.291 | 30.931 | 31.77 | 31.95 | 33.249 |  | 25.4000 | 66.498 | 10.0000
33.249 |  | G33.249x2.309 | G 1 | 11 | B | 33.249 | 32.889 | 31.770 | 31.410 | 30.291
37.897 |  | G37.897x2.309 | G 1 1/8 | 11 | A | 37.897 | 37.537 | 36.418 | 36.238 | 34.939 |  |  | 34.939 | 35.579 | 36.418 | 36.598 | 37.897 |  | 28.5750 | 75.794 | 10.0000
37.897 |  | G37.897x2.309 | G 1 1/8 | 11 | B | 37.897 | 37.537 | 36.418 | 36.058 | 34.939
41.910 |  | G41.91x2.309 | G 1 1/4 | 11 | A | 41.910 | 41.550 | 40.431 | 40.251 | 38.952 |  |  | 38.952 | 39.592 | 40.431 | 40.611 | 41.910 |  | 31.7500 | 83.820 | 10.0000
41.910 |  | G41.91x2.309 | G 1 1/4 | 11 | B | 41.910 | 41.550 | 40.431 | 40.071 | 38.952
47.803 |  | G47.803x2.309 | G 1 1/2 | 11 | A | 47.803 | 47.443 | 46.324 | 46.144 | 44.845 |  |  | 44.845 | 45.485 | 46.324 | 46.504 | 47.803 |  | 38.1000 | 95.606 | 10.0000
47.803 |  | G47.803x2.309 | G 1 1/2 | 11 | B | 47.803 | 47.443 | 46.324 | 45.964 | 44.845
53.746 |  | G53.746x2.309 | G 1 3/4 | 11 | A | 53.746 | 53.386 | 52.267 | 52.087 | 50.788 |  |  | 50.788 | 51.428 | 52.267 | 52.447 | 53.746 |  | 44.4500 | 107.492 | 10.0000
53.746 |  | G53.746x2.309 | G 1 3/4 | 11 | B | 53.746 | 53.386 | 52.267 | 51.907 | 50.788
59.614 |  | G59.614x2.309 | G 2 | 11 | A | 59.614 | 59.254 | 58.135 | 57.955 | 56.656 |  |  | 56.656 | 57.296 | 58.135 | 58.315 | 59.614 |  | 50.8000 | 119.228 | 10.0000
59.614 |  | G59.614x2.309 | G 2 | 11 | B | 59.614 | 59.254 | 58.135 | 57.775 | 56.656
65.710 |  | G65.71x2.309 | G 2 1/4 | 11 | A | 65.710 | 65.276 | 64.231 | 64.014 | 62.752 |  |  | 62.752 | 63.392 | 64.231 | 64.448 | 65.710 |  | 57.1500 | 131.420 | 10.0000
65.710 |  | G65.71x2.309 | G 2 1/4 | 11 | B | 65.710 | 65.276 | 64.231 | 63.797 | 62.752
75.184 |  | G75.184x2.309 | G 2 1/2 | 11 | A | 75.184 | 74.750 | 73.705 | 73.488 | 72.226 |  |  | 72.226 | 72.866 | 73.705 | 73.922 | 75.184 |  |  | 150.368 | 10.0000
75.184 |  | G75.184x2.309 | G 2 1/2 | 11 | B | 75.184 | 74.750 | 73.705 | 73.271 | 72.226
81.534 |  | G81.534x2.309 | G 2 3/4 | 11 | A | 81.534 | 81.100 | 80.055 | 79.838 | 78.576 |  |  | 78.576 | 79.216 | 80.055 | 80.272 | 81.534 |  | 69.8500 | 163.068 | 10.0000
81.534 |  | G81.534x2.309 | G 2 3/4 | 11 | B | 81.534 | 81.100 | 80.055 | 79.621 | 78.576
87.884 |  | G87.884x2.309 | G 3 | 11 | A | 87.884 | 87.450 | 86.405 | 86.188 | 84.926 |  |  | 84.926 | 85.566 | 86.405 | 86.622 | 87.884 |  | 76.2000 | 175.768 | 10.0000
87.884 |  | G87.884x2.309 | G 3 | 11 | B | 87.884 | 87.450 | 86.405 | 85.971 | 84.926
100.330 |  | G100.33x2.309 | G 3 1/2 | 11 | A | 100.330 | 99.896 | 98.851 | 98.634 | 97.372 |  |  | 97.372 | 98.012 | 98.851 | 99.068 | 100.330 |  | 88.9000 | 200.660 | 10.0000
100.330 |  | G100.33x2.309 | G 3 1/2 | 11 | B | 100.330 | 99.896 | 98.851 | 98.417 | 97.372
113.030 |  | G113.03x2.309 | G 4 | 11 | A | 113.030 | 112.596 | 111.551 | 111.334 | 110.072 |  |  | 110.072 | 110.712 | 111.551 | 111.768 | 113.030 |  | 101.6000 | 226.060 | 10.0000
113.030 |  | G113.03x2.309 | G 4 | 11 | B | 113.030 | 112.596 | 111.551 | 111.117 | 110.072
125.730 |  | G125.73x2.309 | G 4 1/2 | 11 | A | 125.730 | 125.296 | 124.251 | 124.034 | 122.772 |  |  | 122.772 | 123.412 | 124.251 | 124.468 | 125.730 |  | 114.3000 | 251.460 | 10.0000
125.730 |  | G125.73x2.309 | G 4 1/2 | 11 | B | 125.730 | 125.296 | 124.251 | 123.817 | 122.772
138.430 |  | G138.43x2.309 | G 5 | 11 | A | 138.430 | 137.996 | 136.951 | 136.734 | 135.472 |  |  | 135.472 | 136.112 | 136.951 | 137.168 | 138.430 |  | 127.0000 | 276.860 | 10.0000
138.430 |  | G138.43x2.309 | G 5 | 11 | B | 138.430 | 137.996 | 136.951 | 136.517 | 135.472
151.130 |  | G151.13x2.309 | G 5 1/2 | 11 | A | 151.130 | 150.696 | 149.651 | 149.434 | 148.172 |  |  | 148.172 | 148.812 | 149.651 | 149.868 | 151.130 |  | 139.7000 | 302.260 | 10.0000
151.130 |  | G151.13x2.309 | G 5 1/2 | 11 | B | 151.130 | 150.696 | 149.651 | 149.217 | 148.172
163.830 |  | G163.83x2.309 | G 6 | 11 | A | 163.830 | 163.396 | 162.351 | 162.134 | 160.872 |  |  | 160.872 | 161.512 | 162.351 | 162.568 | 163.830 |  | 152.4000 | 327.660 | 10.0000
163.830 |  | G163.83x2.309 | G 6 | 11 | B | 163.830 | 163.396 | 162.351 | 161.917 | 160.872

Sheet: DIN Pipe Threads
M Q | DIN Pipe Threads |  | Sort Order - 18 |  | External |  |  |  |  |  |  | Internal
 |  |  |  |  |  | Major Dia |  | Pitch Dia |  | Minor Dia |  |  | Minor Dia |  | Pitch Dia |  | Major Dia |  | Tap Drill | Thread Depth | Thread Runouts
Size | Size Suffix | Thread Designation | Custom Thread Designation | TPI | Class | Max | Min | Max | Min | Max | Min | Class | Min | Max | Min | Max | Min | Max | Basic
7.723 |  | G7.723x0.907 | G 1/16 | 28 | A | 7.723 | 7.509 | 7.142 | 7.035 | 6.561 |  |  | 6.561 | 6.834 | 7.142 | 7.249 | 7.723 |  | 1.5875 | 15.446 | 4.5000
7.723 |  | G7.723x0.907 | G 1/16 | 28 | B | 7.723 | 7.509 | 7.142 | 6.928 | 6.561
9.728 |  | G9.728x0.907 | G 1/8 | 28 | A | 9.728 | 9.514 | 9.147 | 9.040 | 8.566 |  |  | 8.566 | 8.848 | 9.147 | 9.254 | 9.728 |  | 3.1750 | 19.456 | 4.5000
9.728 |  | G9.728x0.907 | G 1/8 | 28 | B | 9.728 | 9.514 | 9.147 | 8.933 | 8.566
13.157 |  | G13.157x1.337 | G 1/4 | 19 | A | 13.157 | 12.907 | 12.301 | 12.176 | 11.445 |  |  | 11.445 | 11.89 | 12.301 | 12.426 | 13.157 |  | 6.3500 | 26.314 | 6.5000
13.157 |  | G13.157x1.337 | G 1/4 | 19 | B | 13.157 | 12.907 | 12.301 | 12.051 | 11.445
16.662 |  | G16.662x1.337 | G 3/8 | 19 | A | 16.662 | 16.412 | 15.806 | 15.681 | 14.950 |  |  | 14.95 | 15.395 | 15.806 | 15.931 | 16.662 |  | 9.5250 | 33.324 | 6.5000
16.662 |  | G16.662x1.337 | G 3/8 | 19 | B | 16.662 | 16.412 | 15.806 | 15.556 | 14.950
20.955 |  | G20.955x1.814 | G 1/2 | 14 | A | 20.955 | 20.671 | 19.793 | 19.651 | 18.631 |  |  | 18.631 | 19.172 | 19.793 | 19.935 | 20.955 |  | 12.7000 | 41.910 | 8.5000
20.955 |  | G20.955x1.814 | G 1/2 | 14 | B | 20.955 | 20.671 | 19.793 | 19.509 | 18.631
22.911 |  | G22.911x1.814 | G 5/8 | 14 | A | 22.911 | 22.627 | 21.749 | 21.607 | 20.587 |  |  | 20.587 | 21.128 | 21.749 | 21.891 | 22.911 |  |  | 45.822 | 8.5000
22.911 |  | G22.911x1.814 | G 5/8 | 14 | B | 22.911 | 22.627 | 21.749 | 21.465 | 20.587
26.441 |  | G26.441x1.814 | G 3/4 | 14 | A | 26.441 | 26.157 | 25.279 | 25.137 | 24.117 |  |  | 24.117 | 24.658 | 25.279 | 25.421 | 26.441 |  | 15.8750 | 52.882 | 8.5000
26.441 |  | G26.441x1.814 | G 3/4 | 14 | B | 26.441 | 26.157 | 25.279 | 24.995 | 24.117
30.201 |  | G30.201x1.814 | G 7/8 | 14 | A | 30.201 | 29.917 | 29.039 | 28.897 | 27.877 |  |  | 27.877 | 28.418 | 29.039 | 29.181 | 30.201 |  | 22.2250 | 60.402 | 8.5000
30.201 |  | G30.201x1.814 | G 7/8 | 14 | B | 30.201 | 29.917 | 29.039 | 28.755 | 27.877
33.249 |  | G33.249x2.309 | G 1 | 11 | A | 33.249 | 32.889 | 31.770 | 31.590 | 30.291 |  |  | 30.291 | 30.931 | 31.77 | 31.95 | 33.249 |  | 25.4000 | 66.498 | 10.5000
33.249 |  | G33.249x2.309 | G 1 | 11 | B | 33.249 | 32.889 | 31.770 | 31.410 | 30.291
37.897 |  | G37.897x2.309 | G 1 1/8 | 11 | A | 37.897 | 37.537 | 36.418 | 36.238 | 34.939 |  |  | 34.939 | 35.579 | 36.418 | 36.598 | 37.897 |  | 28.5750 | 75.794 | 10.5000
37.897 |  | G37.897x2.309 | G 1 1/8 | 11 | B | 37.897 | 37.537 | 36.418 | 36.058 | 34.939
41.910 |  | G41.91x2.309 | G 1 1/4 | 11 | A | 41.910 | 41.550 | 40.431 | 40.251 | 38.952 |  |  | 38.952 | 39.592 | 40.431 | 40.611 | 41.910 |  | 31.7500 | 83.820 | 10.5000
41.910 |  | G41.91x2.309 | G 1 1/4 | 11 | B | 41.910 | 41.550 | 40.431 | 40.071 | 38.952
47.803 |  | G47.803x2.309 | G 1 1/2 | 11 | A | 47.803 | 47.443 | 46.324 | 46.144 | 44.845 |  |  | 44.845 | 45.485 | 46.324 | 46.504 | 47.803 |  | 38.1000 | 95.606 | 10.5000
47.803 |  | G47.803x2.309 | G 1 1/2 | 11 | B | 47.803 | 47.443 | 46.324 | 45.964 | 44.845
53.746 |  | G53.746x2.309 | G 1 3/4 | 11 | A | 53.746 | 53.386 | 52.267 | 52.087 | 50.788 |  |  | 50.788 | 51.428 | 52.267 | 52.447 | 53.746 |  | 44.4500 | 107.492 | 10.5000
53.746 |  | G53.746x2.309 | G 1 3/4 | 11 | B | 53.746 | 53.386 | 52.267 | 51.907 | 50.788
59.614 |  | G59.614x2.309 | G 2 | 11 | A | 59.614 | 59.254 | 58.135 | 57.955 | 56.656 |  |  | 56.656 | 57.296 | 58.135 | 58.315 | 59.614 |  | 50.8000 | 119.228 | 10.5000
59.614 |  | G59.614x2.309 | G 2 | 11 | B | 59.614 | 59.254 | 58.135 | 57.775 | 56.656
65.710 |  | G65.71x2.309 | G 2 1/4 | 11 | A | 65.710 | 65.276 | 64.231 | 64.014 | 62.752 |  |  | 62.752 | 63.392 | 64.231 | 64.448 | 65.710 |  | 57.1500 | 131.420 | 10.5000
65.710 |  | G65.71x2.309 | G 2 1/4 | 11 | B | 65.710 | 65.276 | 64.231 | 63.797 | 62.752
75.184 |  | G75.184x2.309 | G 2 1/2 | 11 | A | 75.184 | 74.750 | 73.705 | 73.488 | 72.226 |  |  | 72.226 | 72.866 | 73.705 | 73.922 | 75.184 |  |  | 150.368 | 10.5000
75.184 |  | G75.184x2.309 | G 2 1/2 | 11 | B | 75.184 | 74.750 | 73.705 | 73.271 | 72.226
81.534 |  | G81.534x2.309 | G 2 3/4 | 11 | A | 81.534 | 81.100 | 80.055 | 79.838 | 78.576 |  |  | 78.576 | 79.216 | 80.055 | 80.272 | 81.534 |  | 69.8500 | 163.068 | 10.5000
81.534 |  | G81.534x2.309 | G 2 3/4 | 11 | B | 81.534 | 81.100 | 80.055 | 79.621 | 78.576
87.884 |  | G87.884x2.309 | G 3 | 11 | A | 87.884 | 87.450 | 86.405 | 86.188 | 84.926 |  |  | 84.926 | 85.566 | 86.405 | 86.622 | 87.884 |  | 76.2000 | 175.768 | 10.5000
87.884 |  | G87.884x2.309 | G 3 | 11 | B | 87.884 | 87.450 | 86.405 | 85.971 | 84.926
100.330 |  | G100.33x2.309 | G 3 1/2 | 11 | A | 100.330 | 99.896 | 98.851 | 98.634 | 97.372 |  |  | 97.372 | 98.012 | 98.851 | 99.068 | 100.330 |  | 88.9000 | 200.660 | 10.5000
100.330 |  | G100.33x2.309 | G 3 1/2 | 11 | B | 100.330 | 99.896 | 98.851 | 98.417 | 97.372
113.030 |  | G113.03x2.309 | G 4 | 11 | A | 113.030 | 112.596 | 111.551 | 111.334 | 110.072 |  |  | 110.072 | 110.712 | 111.551 | 111.768 | 113.030 |  | 101.6000 | 226.060 | 10.5000
113.030 |  | G113.03x2.309 | G 4 | 11 | B | 113.030 | 112.596 | 111.551 | 111.117 | 110.072
125.730 |  | G125.73x2.309 | G 4 1/2 | 11 | A | 125.730 | 125.296 | 124.251 | 124.034 | 122.772 |  |  | 122.772 | 123.412 | 124.251 | 124.468 | 125.730 |  | 114.3000 | 251.460 | 10.5000
125.730 |  | G125.73x2.309 | G 4 1/2 | 11 | B | 125.730 | 125.296 | 124.251 | 123.817 | 122.772
138.430 |  | G138.43x2.309 | G 5 | 11 | A | 138.430 | 137.996 | 136.951 | 136.734 | 135.472 |  |  | 135.472 | 136.112 | 136.951 | 137.168 | 138.430 |  | 127.0000 | 276.860 | 10.5000
138.430 |  | G138.43x2.309 | G 5 | 11 | B | 138.430 | 137.996 | 136.951 | 136.517 | 135.472
151.130 |  | G151.13x2.309 | G 5 1/2 | 11 | A | 151.130 | 150.696 | 149.651 | 149.434 | 148.172 |  |  | 148.172 | 148.812 | 149.651 | 149.868 | 151.130 |  | 139.7000 | 302.260 | 10.5000
151.130 |  | G151.13x2.309 | G 5 1/2 | 11 | B | 151.130 | 150.696 | 149.651 | 149.217 | 148.172
163.830 |  | G163.83x2.309 | G 6 | 11 | A | 163.830 | 163.396 | 162.351 | 162.134 | 160.872 |  |  | 160.872 | 161.512 | 162.351 | 162.568 | 163.830 |  | 152.4000 | 327.660 | 10.5000
163.830 |  | G163.83x2.309 | G 6 | 11 | B | 163.830 | 163.396 | 162.351 | 161.917 | 160.872

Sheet: BSP Pipe Threads
M Q | BSP Pipe Threads |  | Sort Order - 19 |  | External |  |  |  |  |  |  | Internal
 |  |  |  |  |  | Major Dia |  | Pitch Dia |  | Minor Dia |  |  | Minor Dia |  | Pitch Dia |  | Major Dia |  | Tap Drill | Thread Depth | Thread Runouts
Size | Size Suffix | Thread Designation | Custom Thread Designation | TPI | Class | Max | Min | Max | Min | Max | Min | Class | Min | Max | Min | Max | Min | Max | Basic |  | Basic
1/16 |  | G 1/16-28 | G 1/16-28 | 28 | A | 7.723 | 7.509 | 7.142 | 7.035 | 6.561 |  |  | 6.561 | 6.834 | 7.142 | 7.249 | 7.723 |  | 6.6000 | 15.4460 | 4.5000
1/16 |  | G 1/16-28 | G 1/16-28 | 28 | B | 7.723 | 7.509 | 7.142 | 7.035 | 6.561
1/8 |  | G 1/8-28 | G 1/8-28 | 28 | A | 9.728 | 9.514 | 9.147 | 9.040 | 8.566 |  |  | 8.566 | 8.848 | 9.147 | 9.254 | 9.728 |  | 8.7300 | 19.4560 | 4.5000
1/8 |  | G 1/8-28 | G 1/8-28 | 28 | B | 9.728 | 9.514 | 9.147 | 9.040 | 8.566
1/4 |  | G 1/4-19 | G 1/4-19 | 19 | A | 13.157 | 12.907 | 12.301 | 12.176 | 11.445 |  |  | 11.445 | 11.89 | 12.301 | 12.426 | 13.157 |  | 11.8000 | 26.3140 | 6.5000
1/4 |  | G 1/4-19 | G 1/4-19 | 19 | B | 13.157 | 12.907 | 12.301 | 12.176 | 11.445
3/8 |  | G 3/8-19 | G 3/8-19 | 19 | A | 16.662 | 16.412 | 15.806 | 15.681 | 14.950 |  |  | 14.95 | 15.395 | 15.806 | 15.931 | 16.662 |  | 15.2500 | 33.3240 | 6.5000
3/8 |  | G 3/8-19 | G 3/8-19 | 19 | B | 16.662 | 16.412 | 15.806 | 15.681 | 14.950
1/2 |  | G 1/2-14 | G 1/2-14 | 14 | A | 20.955 | 20.671 | 19.793 | 19.651 | 18.631 |  |  | 18.631 | 19.172 | 19.793 | 19.935 | 20.955 |  | 19.0500 | 41.9100 | 8.5000
1/2 |  | G 1/2-14 | G 1/2-14 | 14 | B | 20.955 | 20.671 | 19.793 | 19.651 | 18.631
5/8 |  | G 5/8-14 | G 5/8-14 | 14 | A | 22.911 | 22.627 | 21.749 | 21.607 | 20.587 |  |  | 20.587 | 21.128 | 21.749 | 21.891 | 22.911 |  | 21.0000 | 45.8220 | 8.5000
5/8 |  | G 5/8-14 | G 5/8-14 | 14 | B | 22.911 | 22.627 | 21.749 | 21.607 | 20.587
3/4 |  | G 3/4-14 | G 3/4-14 | 14 | A | 26.441 | 26.157 | 25.279 | 25.137 | 24.117 |  |  | 24.117 | 24.658 | 25.279 | 25.421 | 26.441 |  | 24.5000 | 52.8820 | 8.5000
3/4 |  | G 3/4-14 | G 3/4-14 | 14 | B | 26.441 | 26.157 | 25.279 | 25.137 | 24.117
7/8 |  | G 7/8-14 | G 7/8-14 | 14 | A | 30.201 | 29.917 | 29.039 | 28.897 | 27.877 |  |  | 27.877 | 28.418 | 29.039 | 29.181 | 30.201 |  | 28.2500 | 60.4020 | 8.5000
7/8 |  | G 7/8-14 | G 7/8-14 | 14 | B | 30.201 | 29.917 | 29.039 | 28.897 | 27.877
1 |  | G 1-11 | G 1-11 | 11 | A | 33.249 | 32.889 | 31.770 | 31.590 | 30.291 |  |  | 30.291 | 30.931 | 31.77 | 31.95 | 33.249 |  | 30.7500 | 66.4980 | 10.0000
1 |  | G 1-11 | G 1-11 | 11 | B | 33.249 | 32.889 | 31.770 | 31.590 | 30.291
1 1/4 |  | G 1 1/4-11 | G 1 1/4-11 | 11 | A | 41.910 | 41.550 | 40.431 | 40.251 | 38.952 |  |  | 38.952 | 39.592 | 40.431 | 40.611 | 41.910 |  | 39.5000 | 83.8200 | 10.0000
1 1/4 |  | G 1 1/4-11 | G 1 1/4-11 | 11 | B | 41.910 | 41.550 | 40.431 | 40.251 | 38.952
1 1/2 |  | G 1 1/2-11 | G 1 1/2-11 | 11 | A | 47.803 | 47.443 | 46.324 | 46.144 | 44.845 |  |  | 44.845 | 45.485 | 46.324 | 46.504 | 47.803 |  | 45.5000 | 95.6060 | 10.0000
1 1/2 |  | G 1 1/2-11 | G 1 1/2-11 | 11 | B | 47.803 | 47.443 | 46.324 | 46.144 | 44.845
1 3/4 |  | G 1 3/4-11 | G 1 3/4-11 | 11 | A | 53.746 | 53.386 | 52.267 | 52.087 | 50.788 |  |  | 50.788 | 51.428 | 52.267 | 52.447 | 53.746 |  | 51.0000 | 107.4920 | 10.0000
1 3/4 |  | G 1 3/4-11 | G 1 3/4-11 | 11 | B | 53.746 | 53.386 | 52.267 | 52.087 | 50.788
2 |  | G 2-11 | G 2-11 | 11 | A | 59.614 | 59.254 | 58.135 | 57.955 | 56.656 |  |  | 56.656 | 57.296 | 58.135 | 58.315 | 59.614 |  | 57.0000 | 119.2280 | 10.0000
2 |  | G 2-11 | G 2-11 | 11 | B | 59.614 | 59.254 | 58.135 | 57.955 | 56.656
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

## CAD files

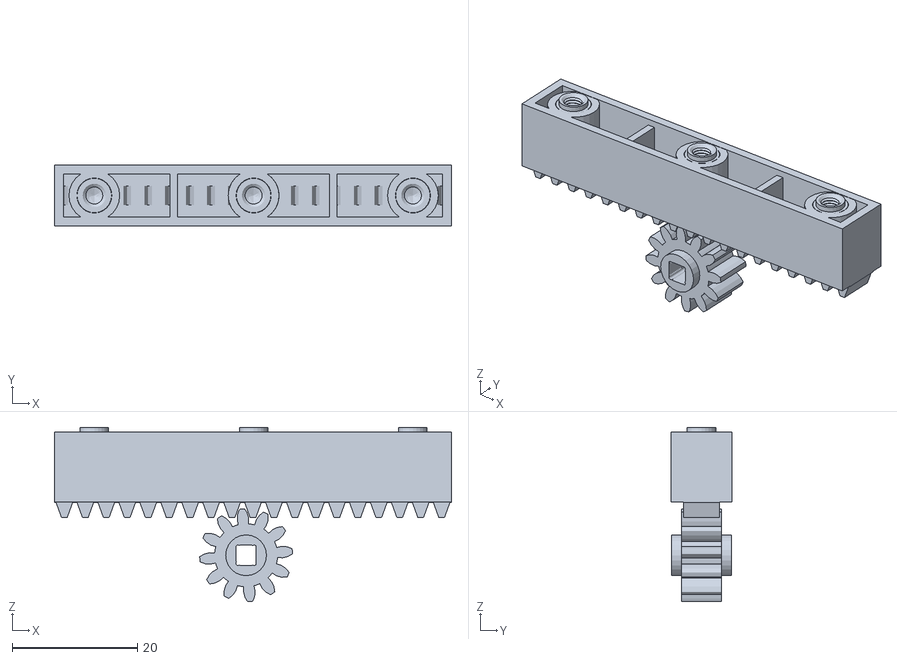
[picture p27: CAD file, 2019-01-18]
Milestones/Milestone 2/CAD Drawings/1e1ed33042fa3d9b8d216efee4ce1745 (1).stl
63.3 x 9.80 x 27.8

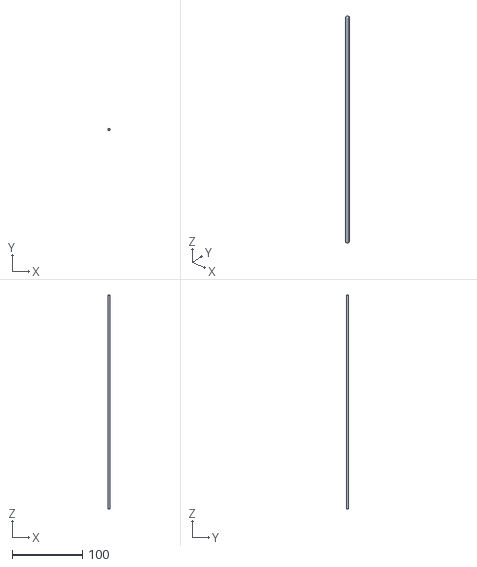
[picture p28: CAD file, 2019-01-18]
Milestones/Milestone 2/CAD Drawings/11fed019d12a415f57fa556b2490bb50.stl
3.17 x 3.17 x 304.8

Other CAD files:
CAD_Drawings/Final assembly/Templates/English/ANSI (in).dwg
CAD_Drawings/Final assembly/Templates/Metric/ANSI (mm).dwg
CAD_Drawings/Final assembly/Templates/Standard.dwg
CAD_Drawings/Small spacer.dwg
Milestones/Renders/Poster condensed explosion-1.dwg
CAD_Drawings/Final assembly/Templates/English/am_ansi.dwg
CAD_Drawings/Final assembly/Templates/Metric/am_jis.dwg
CAD_Drawings/Sidewall.dwg
CAD_Drawings/Back axle.dwg
CAD_Drawings/Final assembly/Templates/Metric/JIS.dwg
CAD_Drawings/Final assembly/Templates/Metric/ISO.dwg
CAD_Drawings/Large Spacer CORRECTED.dwg
CAD_Drawings/Default drawig.dwg
CAD_Drawings/Final assembly/Templates/Metric/GOST.dwg
CAD_Drawings/Final assembly/Templates/Metric/DIN.dwg
CAD_Drawings/Final assembly/Templates/Metric/am_din.dwg
CAD_Drawings/Assembly/Front Axle.ipt
CAD_Drawings/Assembly/Front Gear.ipt
CAD_Drawings/Assembly/motor housing.ipt
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

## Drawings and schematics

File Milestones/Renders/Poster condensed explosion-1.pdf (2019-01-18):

(3)

(2)

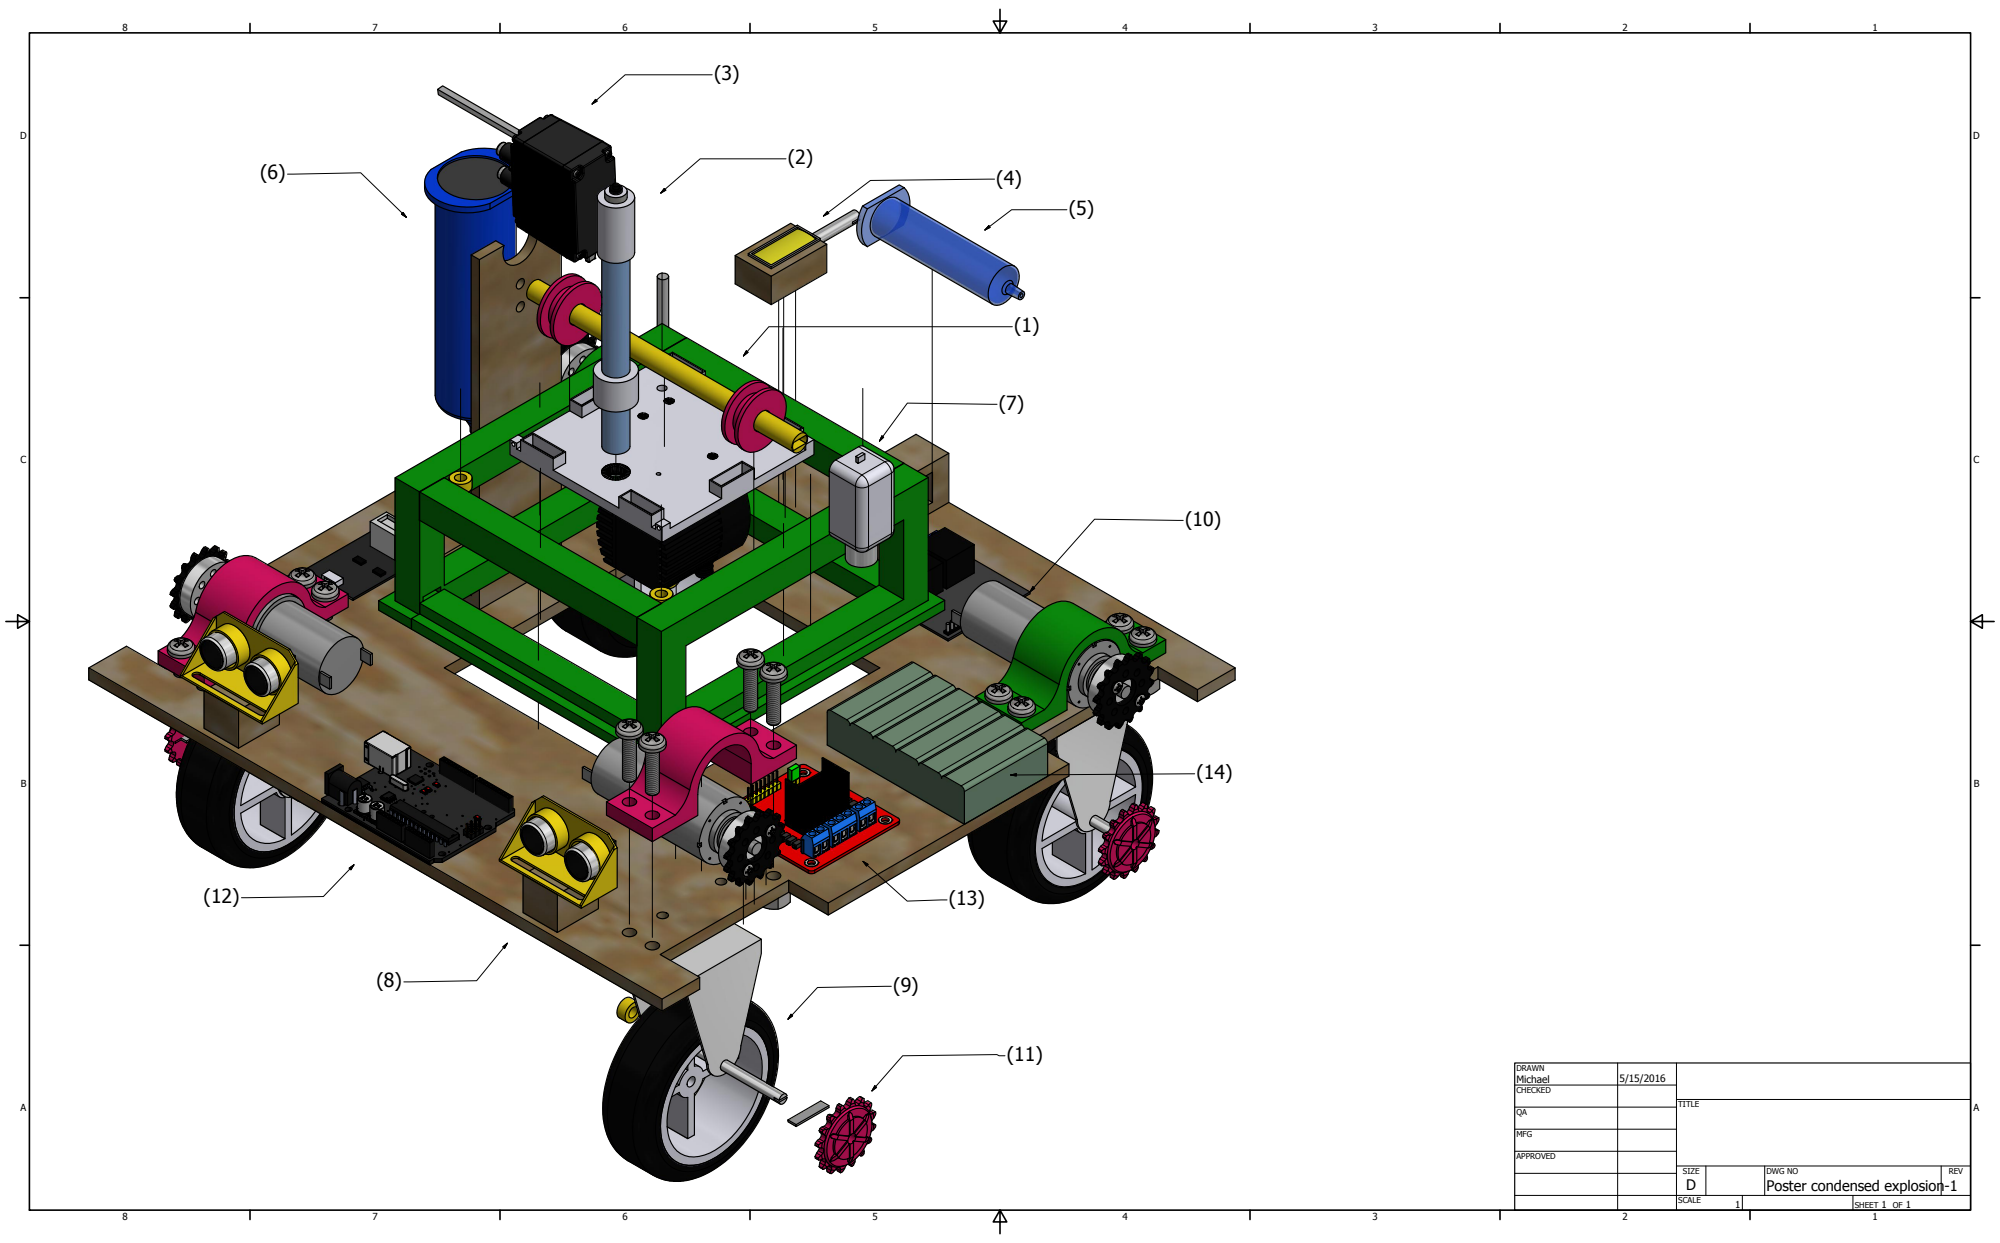
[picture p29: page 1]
SHEET 1 OF 1; DRAWN; CHECKED; MFG; APPROVED; Michael; TITLE; SIZE D; SCALE; REV

DWG NO
Poster condensed explosion-1

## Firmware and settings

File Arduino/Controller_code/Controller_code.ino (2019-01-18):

#include <NewPing.h>
#include "enes100.h"
/* NOTES
 *  Chemical spill location: (2180, 1320)
 */
//Pool positions
#define POOL_X 2.19
#define POOL_Y 1.415

//RF module communications
enes100::RfClient<HardwareSerial> rf(&Serial1);
enes100::Marker marker;

//Sensor pin allocation
#define TRIG_RIGHT 13
#define ECHO_RIGHT 12

#define TRIG_LEFT 16
#define ECHO_LEFT 16
NewPing left(TRIG_LEFT, ECHO_LEFT, 100);
NewPing right(TRIG_RIGHT, ECHO_RIGHT, 100);

//H-Bridge allocations
#define enA 11
#define in1 9
#define in2 8
#define in3 3
#define in4 2
#define enB 10

//On board motor pins
#define ROMEO_E2 6
#define ROMEO_M2 7
#define ROMEO_E1 5
#define ROMEO_M1 4

//pH meter stuff
#define SensorPin A0         //pH meter Analog output to Arduino Analog Input 0
#define Offset 0.06          //deviation compensate

//Relay channels
#define relay_CH1 15
#define relay_CH2 14

//Our Marker ID
#define MARKER_ID 18

//Boolean to describe platform state
boolean platformUp = true;

//Maximum PWM speed for motors
int MAX_SPEED = 255;

//Sort of PID
float thetaDes = 0.0;
float thetaError;

//More constants
int osvSpeed = 100;

void setup() {
  Serial.begin(9600);
  Serial1.begin(9600);
  delay(500);
  pinMode(ROMEO_E2, OUTPUT);
  pinMode(ROMEO_M2, OUTPUT);
  pinMode(ROMEO_M1, OUTPUT);
  pinMode(ROMEO_E1, OUTPUT);
  
  pinMode(enA, OUTPUT);
  pinMode(enB, OUTPUT);
  pinMode(in1, OUTPUT);
  pinMode(in2, OUTPUT);
  pinMode(in3, OUTPUT);
  pinMode(in4, OUTPUT);

  pinMode(relay_CH1, OUTPUT); //For the solenoid
  pinMode(relay_CH2, OUTPUT); //For the stopper remover
  beep(5); //Startup tone
  rf.resetServer();
  rf.sendMessage("\nTeam STS hath arrived.\n");
}

void loop() {
  rf.sendMessage("\nWaiting for marker...\n");
  getMarker();
  rf.sendMessage("\nGot marker!\n");
  moveTo(.50, 1.0); //Move to center of the starting area
  //Code here to determine which path along x axis is clear
  moveTo(1.0, marker.y); //Move to midway x position
  moveTo(POOL_X, POOL_Y); //Move to the pool
  
  //Nudge forward a bit
  move(85);
  delay(100);
  stop();

  baseObjective();
  rf.sendMessage("\nTaking sample\n");
  triggerSolenoid();
  rf.sendMessage("\nWaiting for sample\n");
  for(int i = 0; i <= 20; i++) {
    rf.sendMessage(20 - i);
    delay(1000);
  }
  rf.sendMessage("\nNeutralizing\n");
  stopperMotor();
  pump(true);
  for(int i = 0; i <= 180; i++) {
    rf.sendMessage("\nCurrent pH: \n");
    rf.sendMessage(pH());
    rf.sendMessage("\nTime left: \n");
    rf.sendMessage(180 - i);
    delay(1000);
  }
  rf.sendMessage("\nComplete!\n");
  pump(false);
  raisePlatform();
  while(true){delay(1000);} //Stop the presses!
}

//Moves from current position to a given x, y coordinate
void moveTo(float x, float y) {
  rf.sendMessage("\nAttempting to move to: \n");
  rf.sendMessage(x);
  rf.sendMessage(" , ");
  rf.sendMessage(y);
  int counter = 0;
  while (!atTarget(x, y)) {
    if (counter % 5 == 0) //Does a theta check every so often
      turnToFace(x, y); //Turns to the correct angle
    rf.sendMessage("\n ====MOVING==== \n");
    move(100); //Otherwise move at full speed
    delay(200);
  }
  stop();
  delay(200);
}

//Accepts speeds from -100 to 100
void moveLeft(int speed) {
  speed = map(speed, 0, 100, 0, MAX_SPEED);
  if (speed > 0) {
    digitalWrite(in1, LOW);
    digitalWrite(in2, HIGH);
  }
  if (speed < 0) {
    digitalWrite(in1, HIGH);
    digitalWrite(in2, LOW);
  }
  speed = abs(speed);
  analogWrite(enA, speed);
}

void moveRight(int speed) {
  speed = map(speed, 0, 100, 0, MAX_SPEED);
  if (speed > 0) {
    digitalWrite(in3, LOW);
    digitalWrite(in4, HIGH);
  }
  if (speed < 0) {
    digitalWrite(in3, HIGH);
    digitalWrite(in4, LOW);
  }
  speed = abs(speed);
  analogWrite(enB, speed);
}

void move(int speed) {
  moveRight(speed);
  moveLeft(speed);
}

void stop() {
  move(0);
}

//Converts their theta to a normal theta
float convertTheta(float t) {
  if (t < 0.0) {
    return 6.283 + t;
  }
  return t;
}

//Turns to a theta t
void turnToFace(float x, float y) {
  float td = thetaDesired(x, y);
  if (rf.receiveMarker(&marker, MARKER_ID)) {
    while (fabs(td - convertTheta(marker.theta)) > .2) {
      rf.receiveMarker(&marker, MARKER_ID);
      rf.sendMessage("\nTrying to turn to: \n");
      rf.sendMessage(td);
      rf.sendMessage("\nCurrently at: \n");
      rf.sendMessage(convertTheta(marker.theta));
      float tc = convertTheta(marker.theta);
      float theta;
      float phi;
      if (tc  < td) {
        theta = 6.28 - (td - tc);
        phi = td-tc;
        if (theta < phi) {
          moveLeft(95);
          moveRight(-95);
        }
        if (theta > phi) {
          moveLeft(-95);
          moveRight(95);
        }
      }
      if (tc > td) {
        theta = 6.28 - (tc - td);
        phi = tc - td;
        if (theta < phi) {
          moveLeft(-95);
          moveRight(95);
        }
        if (theta > phi) {
          moveLeft(95);
          moveRight(-95);
        }
      }
      
      td = thetaDesired(x, y); //Update heading
      delay(100);
    }
    stop();
  }
}

//Returns theta desired to get to destination
float thetaDesired(float x, float y) {
  if (getMarker()) {
    float deltaX = x - marker.x;
    float deltaY = y - marker.y; 
    float angle = atan2(deltaY, deltaX);
    if(angle < 0.0)
      return angle + 6.28;
    else {return atan2(deltaY, deltaX);}
  }
}

//Sees if currently close enough to target
boolean atTarget(float x, float y) {
  if (rf.receiveMarker(&marker, MARKER_ID)) {
    float deltaX = fabs(marker.x - x);
    float deltaY = fabs(marker.y - y);
    
    if (deltaX <= .1 && deltaY <= .1)
      return true;
  }
  return false;
}

//MUST BE USED WHEN MARKER IS UPDATED
//Finds distance from current to place
float distanceTo(float x, float y) {
  return sqrt(square(marker.x - x) + square(marker.y - y));
}

void triggerSolenoid() {
  digitalWrite(relay_CH1, HIGH);
  delay(1000);
  digitalWrite(relay_CH1, LOW);
  delay(500);
}

void stopperMotor() {
  digitalWrite(relay_CH2, HIGH);
  delay(2500);
  digitalWrite(relay_CH2, LOW);
  delay(1000);
  pinMode(relay_CH1, INPUT);
}

void baseObjective() {
  Serial.println("Attempting base objective");
  rf.sendMessage("\nAttempting base objective\n");
  beep(3);
  lowerPlatform();
  rf.sendMessage("\nWaiting for pH...\n");
  pump(true);
  delay(10000);
  pump(false);
  rf.sendMessage("\npH: \n");
  rf.sendMessage(pH());
  delay(3000);
}

//Waits for a marker
boolean getMarker() {
  while(!rf.receiveMarker(&marker, MARKER_ID)) {delay(100);}
  return true;
}

//Runs neutralization thing for a while
void neutralize() {
  int timeout = 300; //5 minute timeout (300 seconds)
  pump(true); //Turn on the pump
  stopperMotor(); //Dispense the base
  while (pH() < 6.0) {
    timeout++;
    delay(1000);
  }
  pump(false);
  rf.sendMessage("\nnew pH: \n");
  rf.sendMessage(pH());
}

void lowerPlatform() {
  //Only allows lowering if it hasn't lowered
  if (platformUp) {
    Serial.println("Lowering Platform");
    analogWrite(ROMEO_E2, 75);
    digitalWrite(ROMEO_M2, HIGH);
    delay(2200);
    analogWrite(ROMEO_E2, 0);
  }
  platformUp = false;
}

void raisePlatform() {
  if (!platformUp) {
    Serial.println("Raising Platform");
    analogWrite(ROMEO_E2, 100);
    digitalWrite(ROMEO_M2, LOW);
    delay(2000);
    analogWrite(ROMEO_E2, 80);
    delay(1500);
    analogWrite(ROMEO_E2, 0);
  }
  platformUp = true;
}

//Handles the pump
void pump(boolean engaged) {
  if (engaged) {
    analogWrite(ROMEO_E1, 255);
    digitalWrite(ROMEO_M1, HIGH);
  }
  if (!engaged) {
    analogWrite(ROMEO_E1, 0);
    digitalWrite(ROMEO_M1, HIGH);
  }
}

//Returns distance from right ultrasonic sensor
int rightDist() {
  return right.ping_cm();
}

//Returns distance from left ultrasonic sensor
int leftDist() {
  return left.ping_cm();
}

void printDistances() {
  delay(100);
  Serial.print("Right: ");
  Serial.print(rightDist());
  Serial.print(" cm | ");
  Serial.print("Left: ");
  Serial.print(leftDist());
  Serial.println(" cm");
}

//Returns the measured pH value
float pH() {
  float pHValue,voltage;
  voltage = analogRead(SensorPin) * 5.0/1024.0;
  pHValue = 3.5*voltage+Offset;
  return pHValue;
}

void printPosition() {
  if (rf.receiveMarker(&marker, MARKER_ID)){
    Serial.print("theta: ");
    Serial.println(marker.theta);
    Serial.print("x : ");
    Serial.println(marker.x, 3);
    Serial.print("y: ");
    Serial.println(marker.y, 3);
    Serial.println("");
  }
}

//Plays a number of tones through the motors
void beep(int n) {
  for (int i = 0; i < n; i++) {
    move(25);
    delay(50);
    stop();
    delay(50);
  }
}

//Plays a long and then a short tone
void beep1() {
  move(20);
  delay(500);
  stop();
  delay(100);
  move(20);
  delay(100);
  stop();
}

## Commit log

2019-01-18 Added project files
    [11fed019d12a415f57fa556b2490bb50.stl, 1e1ed33042fa3d9b8d216efee4ce1745 (1).stl, 276-2177-001 Rev1.ipt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]
2019-01-21 Created the README for landing page
